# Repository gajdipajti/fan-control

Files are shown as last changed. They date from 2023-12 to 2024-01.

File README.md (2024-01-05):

# fan-control

A project for controlling 2, 3, and 4 wire DC fans using an Arduino Nano or a Raspberry Pi. It also integrates into munin monitoring. Funded by the [Free Software Foundation Hungary](https://fsf.hu/). The code is under [GPLv3](https://choosealicense.com/licenses/gpl-3.0/). Schematics, drawings, circuit diagrams, and the documentation is under [CC BY-SA-4.0](https://creativecommons.org/licenses/by-sa/4.0/). If you have an idea about how to improve the project, just file an issue and contribute.

## Pages

* [Bill Of Materials](bom/billofmaterials-nano.md)
* [Datasheet Archive](bom/datasheets.md)
* [KiCad and Fritzing](circuits/)

## Wiki

In **hungarian** and in **english**: [wiki](https://github.com/gajdipajti/fan-control/wiki)

## Fan Control Nano - Schematic

*Note: There are multiple solutions displayed here, only implement the needed ones.*

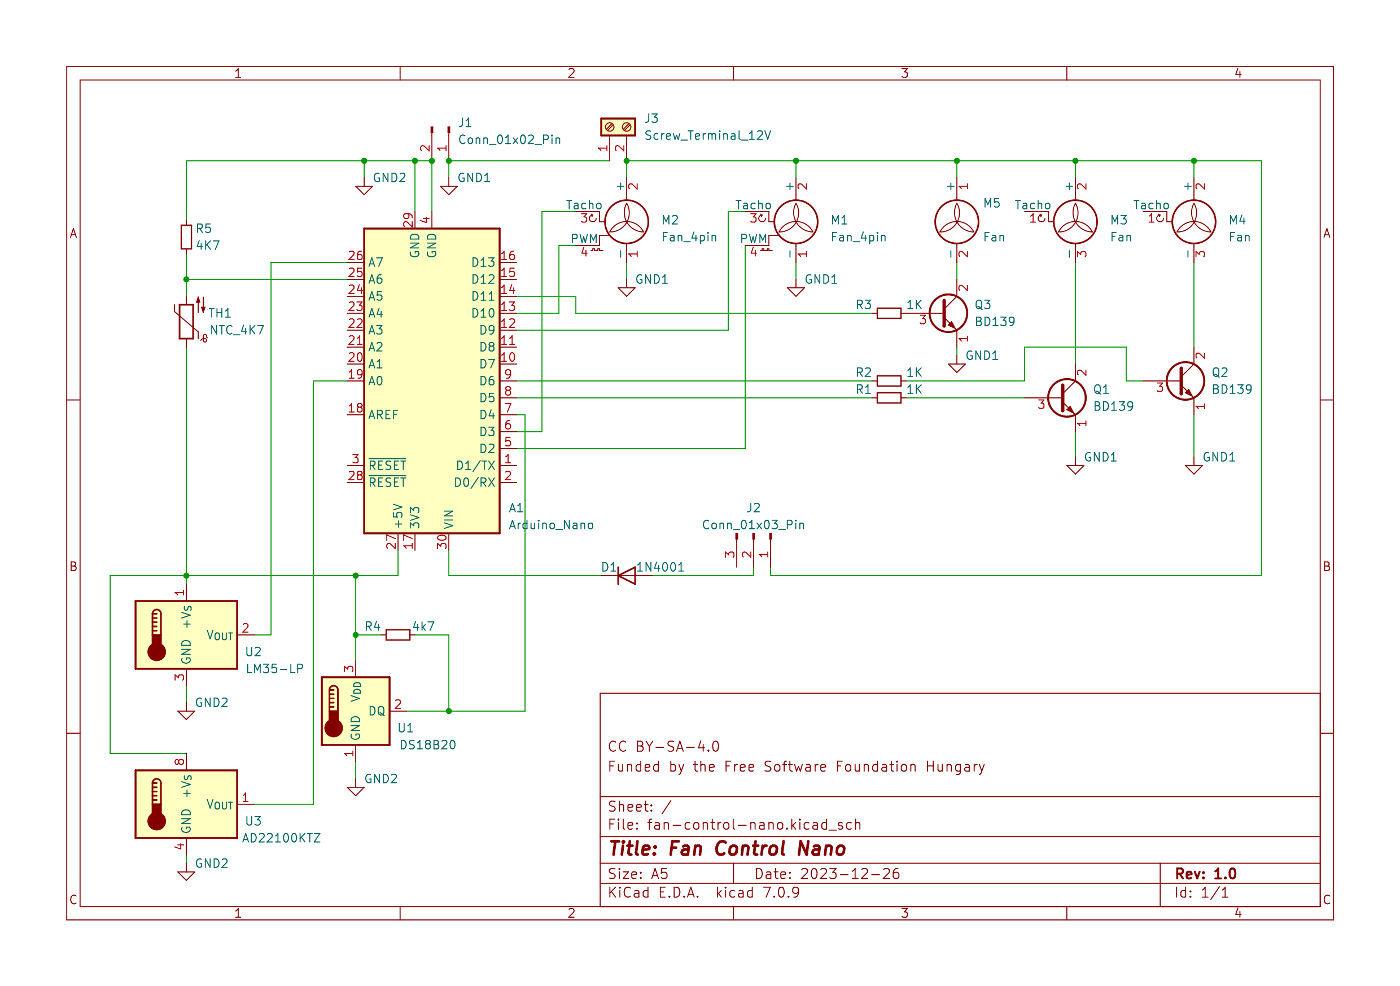
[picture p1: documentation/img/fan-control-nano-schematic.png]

How to start placing the components
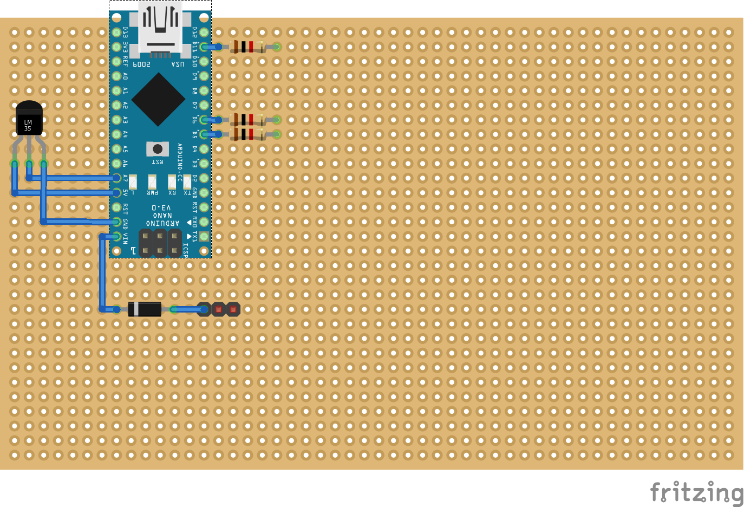
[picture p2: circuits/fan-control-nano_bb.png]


## Fan Control Nano - Code

* [Arduino Nano Code](fan-control-nano/fan-control-nano.ino)

### Serial communication

* 115200 bps
* Main Functions:
  * **pwm?**             - GET all PWM outputs
  * **pwm[A-F]?**        - GET PWM output
  * **pwm[A-F]p**        - SET PWM output to pilot mode
  * **pwm[A-F][0-255]**  - SET PWM output manually
  * **rpm[C,D]?**        - GET RPM output from 4-wire fans
  * **t?**               - GET measured temperature
  * **t[A,D,L,N]?**      - GET measured temperature from selected source
  * **ts?**              - GET temperature source (example Dallas 1-wire)
  * **tsa?**             - GET all available temperature sources
* Calibration Functions:
  * **Ch[L,H,C][A-F]?**        - GET LOW HIGH temperature for a channel
  * **Ch[L,H,C][A-F][0-100]**  - SET LOW HIGH temperature for a channel
  * **p[L,H][A-F]?**           - GET LOW HIGH PWM speed for a channel
  * **p[L,H][A-F][0-255]**     - SET LOW HIGH PWM for a channel
* Misc Func:
  * **hrs?**           - get board uptime [%d:%H:%M:%S]
  * **ver?**           - HW board version number
  * **cbn?**           - CODE build version number
  * **?**              - Ping, Are You There?  + Flash a LED

## Fan Control RPi - Schematic

*Note: There are multiple solutions displayed here, only implement the needed ones.*

*Note: Under testing.*

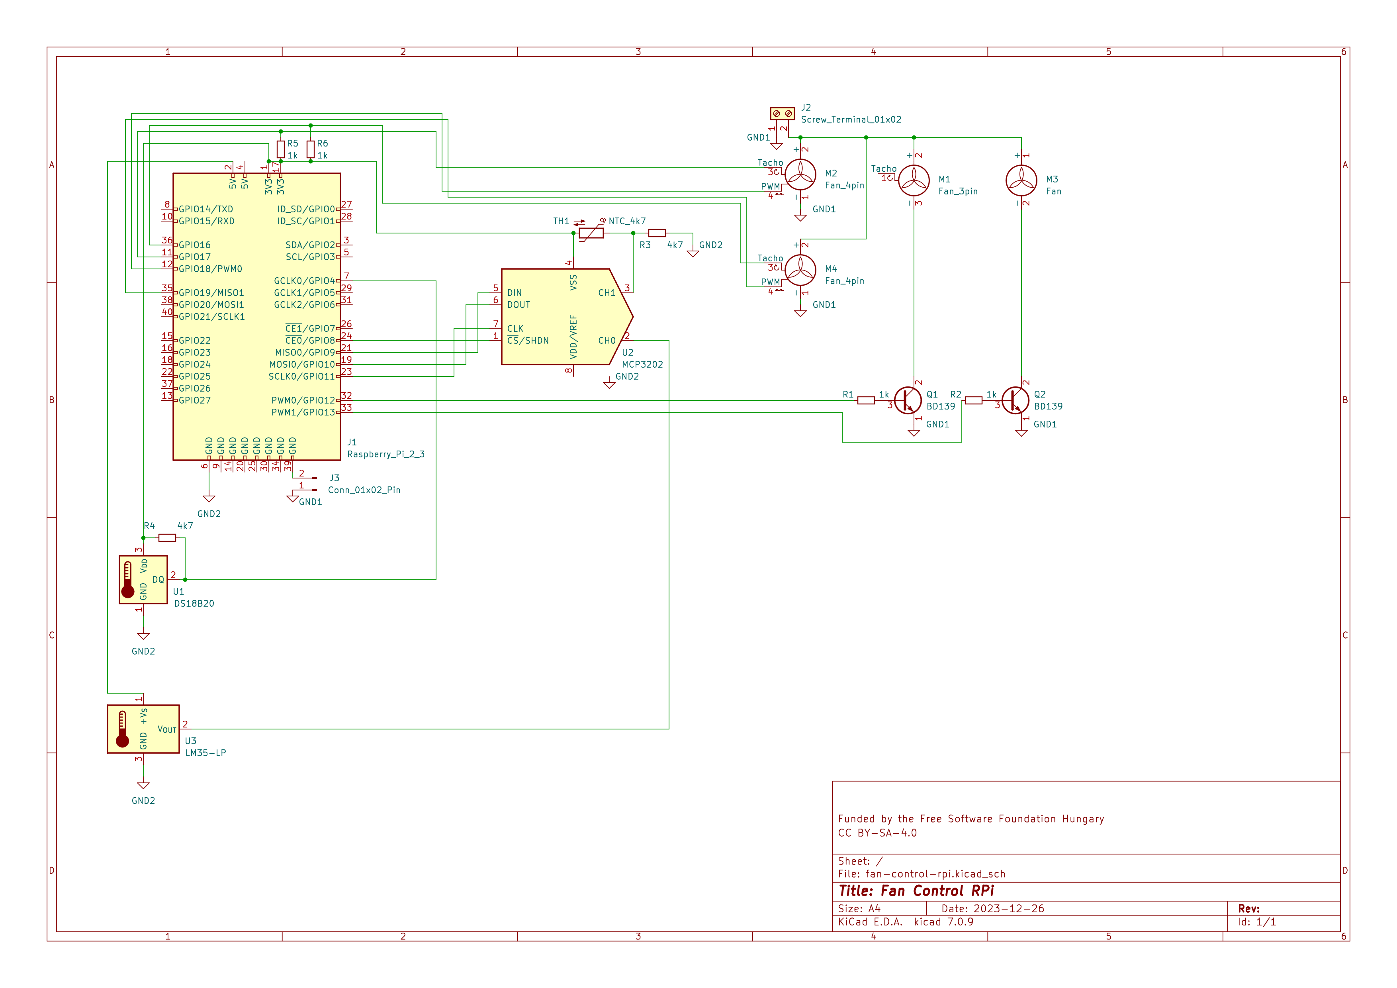
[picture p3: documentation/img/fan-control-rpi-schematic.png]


## Planned updates

* External ADC experiments
* Other board support (RP2040, Attiny85, ...)
* Without machine spirit (no microcontroller)

## References

* [Arduino Language Reference](https://www.arduino.cc/reference/en/)
  * [attachInterrupt()](https://www.arduino.cc/reference/en/language/functions/external-interrupts/attachinterrupt/)
  * [interrupts](http://gammon.com.au/interrupts)
  * [libraries](https://www.arduino.cc/reference/en/libraries/)
* [Arduino Nano](https://docs.arduino.cc/hardware/nano)
* [1-wire protocol](https://docs.arduino.cc/learn/communication/one-wire)
* [Raspberry Pi documentation](https://www.raspberrypi.com/documentation/computers/raspberry-pi.html)
* [Raspberry gpiozero](https://gpiozero.readthedocs.io/en/stable/index.html)
  * [gpiozero - pwmoutput](https://gpiozero.readthedocs.io/en/stable/api_output.html#pwmoutputdevice)
* [Raspberry Pi Zero 2 W Pinout](https://linuxhint.com/raspberry-pi-zero-2w-pinout/)
* [RPI Zero 2W Board Layout](https://www.etechnophiles.com/rpi-zero-2w-board-layout-pinout-specs-price/)

### Free Software used in this project

*Note: I only mention software that can be downloaded and installed.*

* [LibreOffice Writer](https://www.libreoffice.org/) - documentation
* [Visual Studio Code](https://code.visualstudio.com/) - documentation
  * [Markdown All in One](https://marketplace.visualstudio.com/items?itemName=yzhang.markdown-all-in-one)
  * [Markdown PDF](https://marketplace.visualstudio.com/items?itemName=yzane.markdown-pdf)
  * [markdownlint](https://marketplace.visualstudio.com/items?itemName=DavidAnson.vscode-markdownlint)
  * [Remote - SSH](https://marketplace.visualstudio.com/items?itemName=ms-vscode-remote.remote-ssh)
  * [Remote - SSH: Editing Configuration Files](https://marketplace.visualstudio.com/items?itemName=ms-vscode-remote.remote-ssh-edit)
  * [Remote Explorer](https://marketplace.visualstudio.com/items?itemName=ms-vscode.remote-explorer)
  * [Winter is Coming Theme](https://marketplace.visualstudio.com/items?itemName=johnpapa.winteriscoming) - Dark Blue
  * [Cyberpunk Theme](https://marketplace.visualstudio.com/items?itemName=max-SS.cyberpunk) - UMBRA Protocol
  * [Code Spell Checker](https://marketplace.visualstudio.com/items?itemName=streetsidesoftware.code-spell-checker)
  * [isort](https://marketplace.visualstudio.com/items?itemName=ms-python.isort)
  * [Pylance](https://marketplace.visualstudio.com/items?itemName=ms-python.vscode-pylance)
  * [Python](https://marketplace.visualstudio.com/items?itemName=ms-python.python)
* [Arduino IDE](https://www.arduino.cc/en/software) - Arduino code
  * [OneWire](https://www.arduino.cc/reference/en/libraries/onewire/)
  * [DallasTemperature](https://www.arduino.cc/reference/en/libraries/dallastemperature/)
* [KiCad](https://www.kicad.org/download/) - schematics
* [Fritzing](https://github.com/fritzing/fritzing-app/releases/tag/CD-548) - schematics
* [GNU Octave](https://octave.org/) - drawing graphs, advanced calculations
* [Qalculate!](http://qalculate.github.io/) - basic calculation

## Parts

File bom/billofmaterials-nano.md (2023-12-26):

# Bill Of Materials for the Arduino Nano and Raspberry Pi based fan controller

All the materials except the Arduino Nano v3 and the Raspberry Pi was bought from a local supplier: [Robotron Electronika](https://www.ret.hu/) - [pdf catalogue](https://www.ret.hu/FlippingBook/files/assets/downloads/files/RETKAT2012.pdf)

I also included RS links, where possible

## Arduino and Board

* 1x Arduino Nano v3 - [welectron AI-100005](https://www.welectron.com/Arduino-Nano_1), [RS 6961667](https://uk.rs-online.com/web/p/products/6961667/) - 19.99 Euro/piece - (can be replaced with a clone)
* 1x female header BL1-036-G700-95 - [RET 53-03-04](https://www.ret.hu/shop/product/e-tec/36g-buchsenleiste_53-03-04) - 1199 HUF/piece
* 1x 1N 4001 diode - [RET 19-00-01](https://www.ret.hu/shop/product/diotec/1n-4001_19-00-01), [RS 628-8931](https://uk.rs-online.com/web/p/schottky-diodes-rectifiers/6288931) - 18 HUF

## Raspberry Pi and Board

* Raspberry Pi Zero 2 W - [welectron RP1-120008](https://www.welectron.com/Raspberry-Pi-Zero-2-W_1) - 22.90 Euro/piece
* 1x male-female header BE2-040-S161-55 [RET 53-10-01](https://www.ret.hu/shop/product/e-tec/2-x-20g-16mm-buchsenleiste_53-10-01) - 1439 HUF/piece
* 1x male header SL2-050-S116/01-55 [RET 53-00-14](https://www.ret.hu/shop/product/e-tec/2-x-25g-stiftleiste_53-00-14) - 239 HUF/piece
* 1x MCP3201 single channel A/D converter [RET 38-31-67](https://www.ret.hu/shop/product/microchip/mcp-3201-ci-p_38-31-67) - 2999 HUF/piece (_if needed_)

## Board

* 1x H25PR050 single sided proto board - [RET 75-00-15](https://www.ret.hu/shop/product/rademacher/h25pr050_75-00-15) - 575 HUF/piece
* 1x male header SL1-036-SH116/01-55 - [RET 53-03-27](https://www.ret.hu/shop/product/e-tec/36g-stiftleiste_53-03-27) - 179 HUF/piece
* 2x Jumper - [RET 53-14-29](https://www.ret.hu/shop/product/taiwan-king-pin-terminal/jumper-zart-fekete_53-14-29) - 29 HUF/piece
* 1x terminal [RET 53-05-69](https://www.ret.hu/shop/product/ptr-messtechnik/ak-500-2v_53-05-69) - 114 HUF/piece

## Temperature sensing

*Note: One sensor is enough.*

* 2x 4K7 Ohm 1% Resistor - [RET 02-02-39](https://www.ret.hu/shop/product/yageo/4-7-kohm-0-66w-1-rm4_02-02-39), [RS 199-7654](https://uk.rs-online.com/web/p/through-hole-resistors/1997654) - 18 HUF/piece
* 1x DS18B20 sensor - [RET 38-22-36](https://www.ret.hu/shop/product/dallas/ds-18b20_38-22-36) - 1260 HUF/piece
* 1x NTC 4K7 3950 thermistor - [RET 09-00-34](https://www.ret.hu/shop/product/tdk-epcos/4-7-kohm-ntc-rm2-d-5-5mm_09-00-34), [RS 191-2257](https://uk.rs-online.com/web/p/thermistor-ics/1912257) - 336 HUF/piece
* 1x LM35 sensor - [RET 38-06-26](https://www.ret.hu/shop/product/national-semiconductor/lm-35dz-nopb_38-06-26), [533-5878](https://uk.rs-online.com/web/p/temperature-humidity-sensor-ics/5335878) - 1319 HUF/piece

## Fan interfacing

* 3x 1K Ohm 5% Resistor - [RET 01-00-73](https://www.ret.hu/shop/product/yageo/1-kohm-0-25w-5-rm4_01-00-73), [RS 199-1785](https://uk.rs-online.com/web/p/through-hole-resistors/1991785P) - 6 HUF/piece
* 3x NPN Transistor BD139-16 - [RET 24-03-30](https://www.ret.hu/shop/product/continental-devices/bd-139-16-n_24-03-30), [RS 686-8063](https://uk.rs-online.com/web/p/bipolar-transistors/6868063) - 106 HUF/piece
* 2x 4 pin fan header - [RET 53-32-25](https://www.ret.hu/shop/product/molex/22-27-2041_53-32-25), [RS 483-8483](https://uk.rs-online.com/web/p/products/4838483/)  - 478 HUF/piece
* 3x 3 pin fan header - [RET 53-34-30](https://www.ret.hu/shop/product/molex/22-27-2031_53-34-30), [RS 483-8477](https://uk.rs-online.com/web/p/products/4838477/)
* 3x 2 pin fan header - [RET 53-34-29](https://www.ret.hu/shop/product/molex/22-27-2021_53-34-29), [RS 483-8461](https://uk.rs-online.com/web/p/products/4838461/)

## RET Cart for the Nano version (in hungarian)

| Sorszám | Termékkód | Termék | Egységár (Nettó) | Egységár (Bruttó) | Mennyiség | Összesen (Nettó) | Összesen (Bruttó) |
| --- | --- | --- | --- | --- | --- | --- | --- |
| 1 | [09-00-34](https://www.ret.hu/shop/product/tdk-epcos/4-7-kohm-ntc-rm2-d-5-5mm_09-00-34) | 4.7 KOhm, NTC RM2 D=5,5mm | 264.57 HUF | 336 HUF | 1 | 264.57 HUF | 336 HUF |
| 2 | [75-00-15](https://www.ret.hu/shop/product/rademacher/h25pr050_75-00-15) | H25PR050 | 452.59 HUF | 574.79 HUF | 1 | 452.59 HUF | 574.79 HUF |
| 3 | [38-22-36](https://www.ret.hu/shop/product/dallas/ds-18b20_38-22-36) | DS 18B20+ | 992.12 HUF | 1259.99 HUF | 1 | 992.12 HUF | 1259.99 HUF |
| 4 | [24-03-30](https://www.ret.hu/shop/product/continental-devices/bd-139-16-n_24-03-30) | BD 139-16 \*N | 83.15 HUF | 105.6 HUF | 3 | 249.45 HUF | 316.8 HUF |
| 5 | [02-02-39](https://www.ret.hu/shop/product/yageo/4-7-kohm-0-66w-1-rm4_02-02-39) | 4.7 KOhm 0.66W 1% RM4 | 14.17 HUF | 18 HUF | 2 | 28.34 HUF | 35.99 HUF |
| 6 | [01-00-73](https://www.ret.hu/shop/product/yageo/1-kohm-0-25w-5-rm4_01-00-73) | 1 KOhm 0.25W 5% RM4 | 4.72 HUF | 5.99 HUF | 3 | 14.16 HUF | 17.98 HUF |
| 7 | [19-00-01](https://www.ret.hu/shop/product/diotec/1n-4001_19-00-01) | 1N 4001 | 14.17 HUF | 18 HUF | 1 | 14.17 HUF | 18 HUF |
| 8 | [53-03-04]((https://www.ret.hu/shop/product/e-tec/36g-buchsenleiste_53-03-04)) | 36G Buchsenleiste | 943.95 HUF | 1198.82 HUF | 1 | 943.95 HUF | 1198.82 HUF |
| 9 | [53-14-29](https://www.ret.hu/shop/product/taiwan-king-pin-terminal/jumper-zart-fekete_53-14-29)  | JUMPER zárt fekete | 22.68 HUF | 28.8 HUF | 2 | 45.36 HUF | 57.61 HUF |
| 10 | [53-05-69](https://www.ret.hu/shop/product/ptr-messtechnik/ak-500-2v_53-05-69) | AK 500/2V | 89.76 HUF | 114 HUF | 1 | 89.76 HUF | 114 HUF |
| 11 | [38-06-26](https://www.ret.hu/shop/product/national-semiconductor/lm-35dz-nopb_38-06-26) | LM 35DZ/NOPB | 1038.42 HUF | 1318.79 HUF | 1 | 1038.42 HUF | 1318.79 HUF |
| 12 | [53-32-25](https://www.ret.hu/shop/product/molex/22-27-2041_53-32-25) | 22-27-2041 | 188.03 HUF | 238.8 HUF | 2 | 376.06 HUF | 477.6 HUF |
| 13 | [53-34-30](https://www.ret.hu/shop/product/molex/22-27-2031_53-34-30) | 22-27-2031 | 0 HUF | 0 HUF | 3 | 0 HUF | 0 HUF |
| 14 | [53-34-29]((https://www.ret.hu/shop/product/molex/22-27-2021_53-34-29)) | 22-27-2021 | 0 HUF | 0 HUF | 3 | 0 HUF | 0 HUF |
| 15 | [53-03-27](https://www.ret.hu/shop/product/e-tec/36g-stiftleiste_53-03-27) | 36G Stiftleiste | 140.79 HUF | 178.8 HUF | 1 | 140.79 HUF | 178.8 HUF |
| | | | | | | | |
| | | | | | | Nettó összesen | Bruttó összesen |
| | | | | | | 4650 HUF | 5905 HUF |

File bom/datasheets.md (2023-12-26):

# Datasheet Archive for the project

Note: this is just a datasheet archive of the electronic components that are mentioned

## Fan Control Nano

* Diode [1N4001](datasheet-archive-nano/1n4001.pdf)
* Transistor [BD139](datasheet-archive-nano/bd139.pdf) or [BD139](datasheet-archive-nano/bd135_37_39.pdf)
* Resistor 4k7 1% [Yageo MF0207FTE52-4K7](datasheet-archive-nano/Yageo_LR_MF0207FTE52-4K7.pdf)
* Resistor 1k 5% [Yageo CFR-25JT-52-1K](datasheet-archive-nano/Yageo_LR_CFR-25JT-52-1K.pdf)
* Temperature sensor [Maxim DS18B20](datasheet-archive-nano/DS18B20.pdf)
* Thermistor [NTC 4k7 3950](datasheet-archive-nano/Epcos_B57164K.pdf)
* Temperature sensor [TI LM35DZ](datasheet-archive-nano/lm35.pdf)

## Fan Control RPi

* Diode [1N4001](datasheet-archive-nano/1n4001.pdf)
* Transistor [BD139](datasheet-archive-nano/bd139.pdf) or [BD139](datasheet-archive-nano/bd135_37_39.pdf)
* Resistor 4k7 1% [Yageo MF0207FTE52-4K7](datasheet-archive-nano/Yageo_LR_MF0207FTE52-4K7.pdf)
* Resistor 1k 5% [Yageo CFR-25JT-52-1K](datasheet-archive-nano/Yageo_LR_CFR-25JT-52-1K.pdf)
* Temperature sensor [Maxim DS18B20](datasheet-archive-nano/DS18B20.pdf)
* Thermistor [NTC 4k7 3950](datasheet-archive-nano/Epcos_B57164K.pdf)
* Temperature sensor [TI LM35DZ](datasheet-archive-nano/lm35.pdf)
* A/D Converter Microchip [MCP3002](datasheet-archive-misc/mcp3002.pdf)

## Microchip A/D converters (SPI)

* [MCP3001](datasheet-archive-misc/mcp3001.pdf)
* [MCP3002](datasheet-archive-misc/mcp3002.pdf)
* [MCP3004/8](datasheet-archive-misc/mcp300x.pdf)
* [MCP3201](datasheet-archive-misc/mcp3201.pdf)
* [MCP3202](datasheet-archive-misc/mcp3202.pdf)
* [MCP3204/8](datasheet-archive-misc/mcp320x.pdf)

## Other components that were considered

* Temperature sensor [AD22100](datasheet-archive-misc/AD22100.pdf) - only positive values, large range
* Transistor [2N3904](datasheet-archive-misc/2N3903-D.PDF) - less power
* Voltage reference 1.235 Volt [LM385-1.2](datasheet-archive-misc/LM285-D.PDF)
* Voltage reference 2.5 Volt [LM385-2.5](datasheet-archive-misc/LM285-D.PDF) or [LM385-2.5-N](datasheet-archive-misc/lm285-2.5-n.pdf)
* Voltage reference 5.0 Volt [LM336](datasheet-archive-misc/lm336-5.0.pdf)
* Voltage converter 5.0 Volt 1 Amp [L7805](datasheet-archive-misc/L7805.pdf)
* Voltage converter 5.0 Volt 1 Amp [LM2940-5](datasheet-archive-misc/lm2940-n.pdf)

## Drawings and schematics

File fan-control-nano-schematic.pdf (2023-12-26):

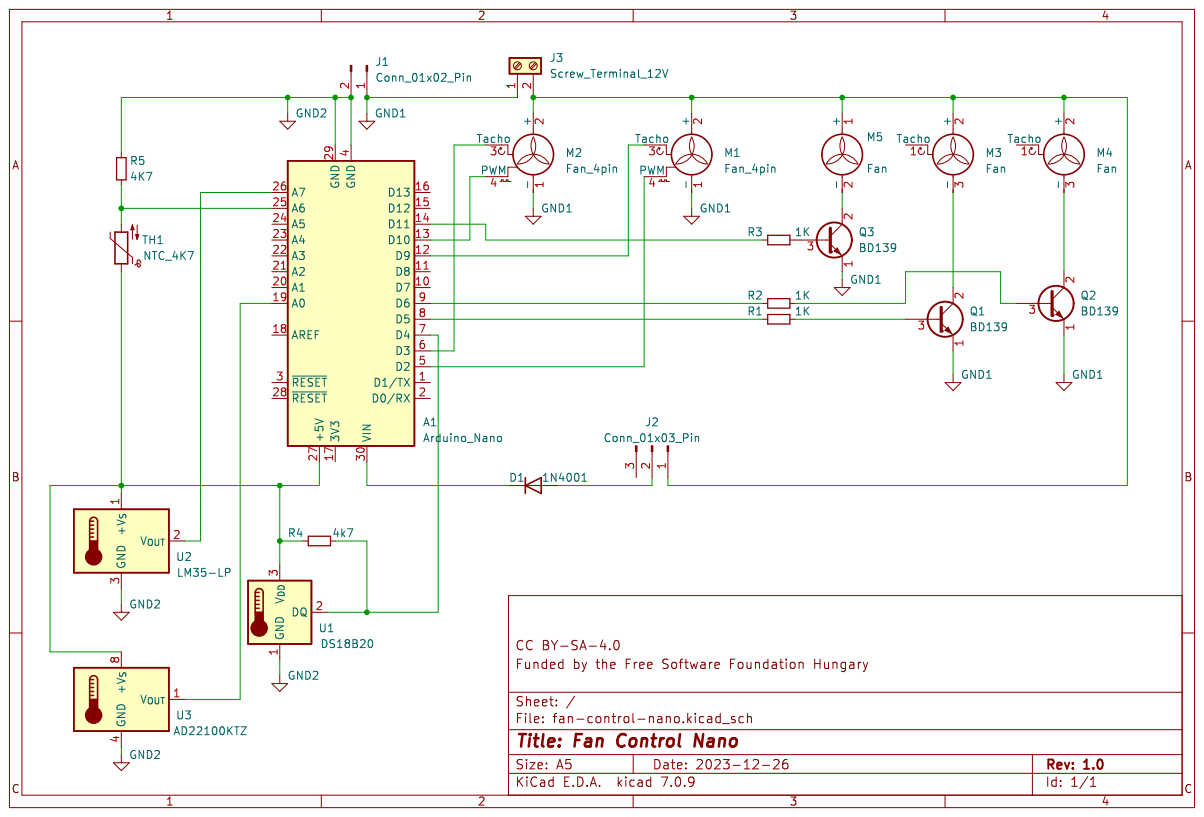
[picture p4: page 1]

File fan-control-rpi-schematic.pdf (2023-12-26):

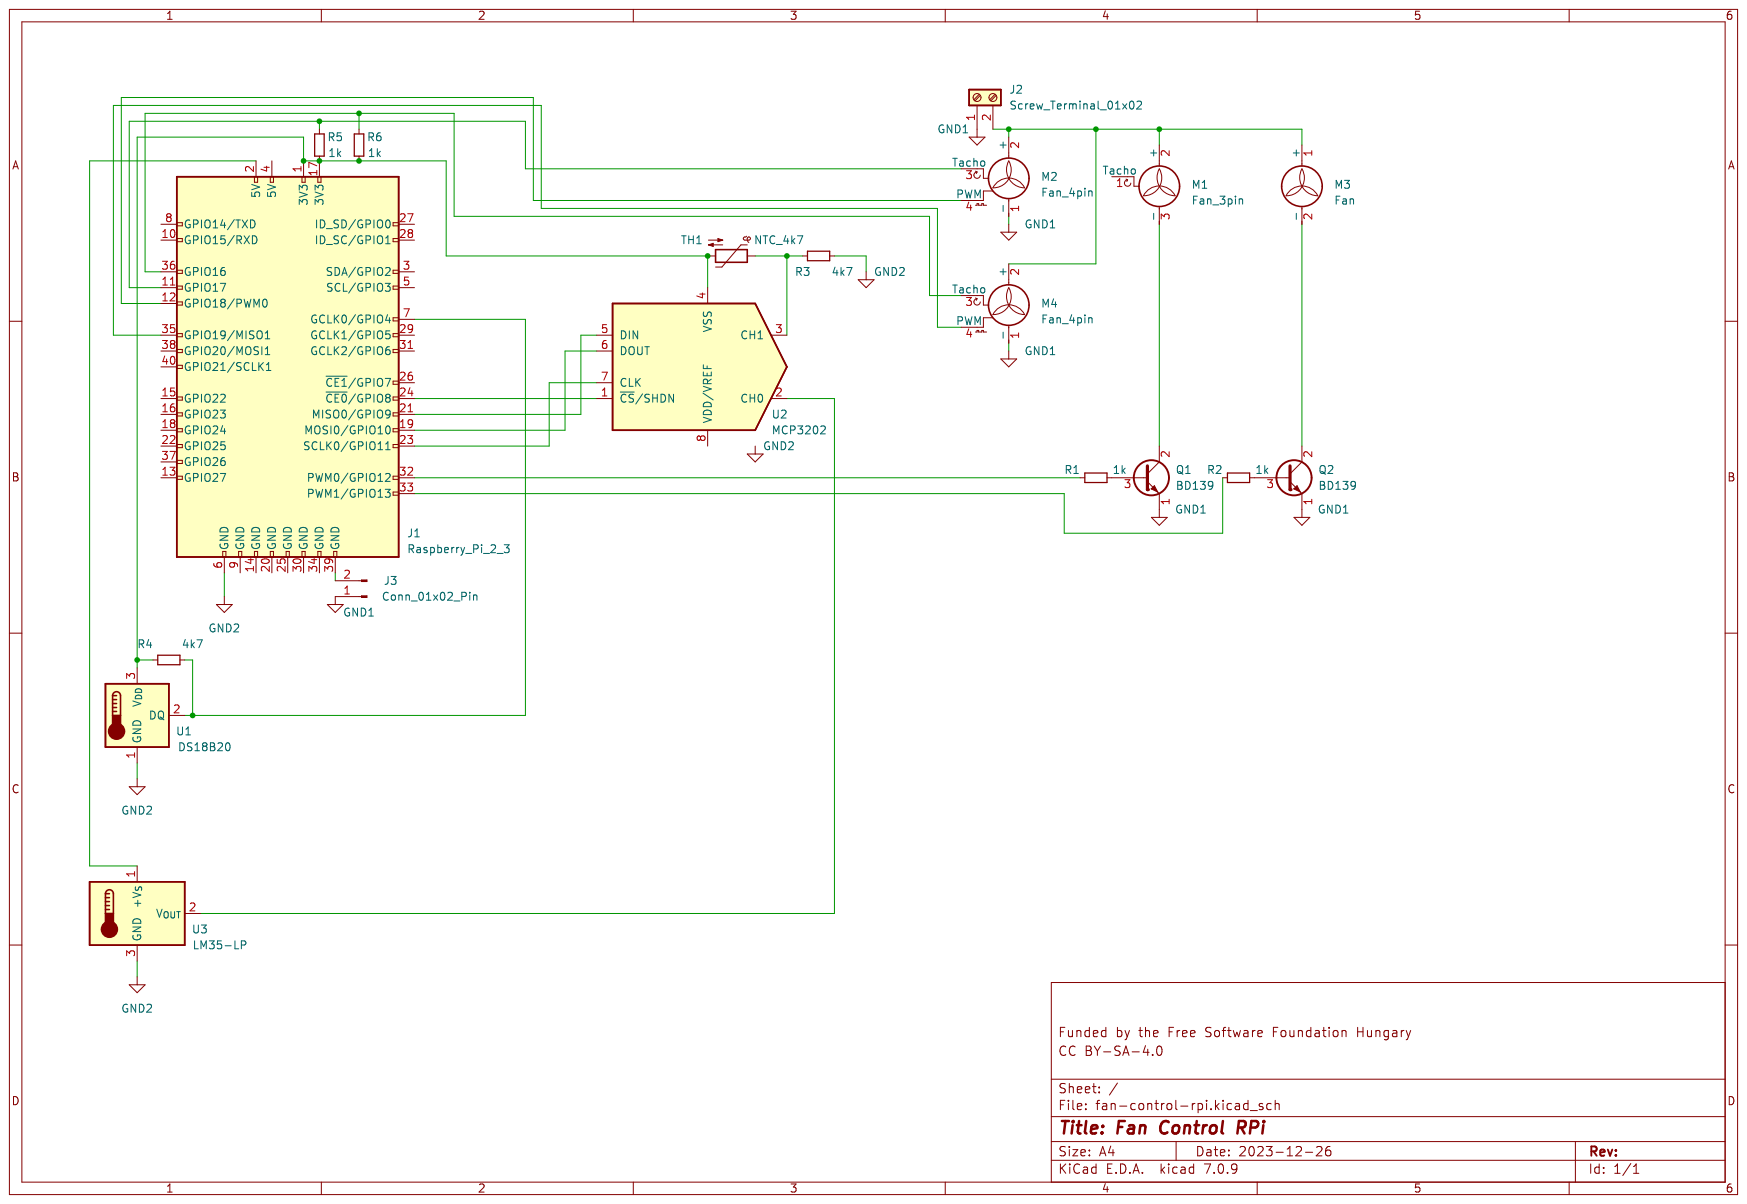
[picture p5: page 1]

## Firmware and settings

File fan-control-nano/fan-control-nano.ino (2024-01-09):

/*
  A 5 channel fan controller for 2, 3, and 4 wire fans.
  Code under GPLv3 license. Author: gajdost (gajdipajti@gmail.com)

Pin Assignment:

  Fan channels: 
   * PIN D5  (Timer0) PWM - ChA - 2 or 3 pin fans only
   * PIN D6  (Timer0) PWM - ChB - 2 or 3 pin fans only
   * PIN D9  (Timer1) PWM - ChC - configured for 4 pin fan
   * PIN D10 (Timer1) PWM - ChD - configured for 4 pin fan
   * PIN D11 (Timer2) PWM - ChE - 2, 3, or 4 pin fans
  Optional fan channel:
   * PIN D3  (Timer2) PWM - ChF - 2, 3, or 4 pin fans OR tachometer interrupt

  Detect interrupts:
   * PIN D2           Tachometer - Interrupt ChC
   * PIN D3  (Timer2) Tachometer - Interrupt ChD

  Temperature measurement (one is enough):
   * PIN D12          Dallas 1-wire DS18B20
   * PIN A7  (ADC)    LM35
   * PIN A6  (ADC)    NTC Thermistor - NTC B57164K0472K000 Rn: 4k7 Ohm; K = 3950; Rs = 4k7 Ohm
   * PIN A0  (ADC)    AD22100KTZ
  Optional temperature pins:
   * PIN A1  (ADC) - tE
   * PIN A2  (ADC) - tD
   * PIN A3  (ADC) - tC

  Optional display pins:
   * PIN D4        - button press
   * PIN A4  (LCD) - reserved for I2C
   * PIN A5  (LCD) - reserved for I2C

  Heartbeat pin:
   * PIN D13 (LED) - heartbeat

Serial Commands:

  Main Functions:
   * fan?             - GET installed fans, all information
   * pwm?             - GET all PWM outputs
   * pwm[A-F]?        - GET PWM output
   * pwm[A-F]p        - SET PWM output to pilot mode
   * pwm[A-F][0-255]  - SET PWM output manually
   * rpm[C,D]?        - GET RPM output from 4-wire fans
   * t?               - GET measured temperature
   * t[A,D,L,N]?        - GET measured temperature from selected source
   * ts?              - GET temperature source (example Dallas 1-wire)
   * tsa?             - GET all available temperature sources

  Optional Functions: [when extra circuit is present]
   * lcd[?,0-4] - GET/SET LCD Backlight; Update LCD
  Calibration Functions:
   * Ch[L,H,C][A-F]?        - GET LOW HIGH temperature for a channel
   * Ch[L,H,C][A-F][0-100]  - SET LOW HIGH temperature for a channel
   * p[L,H][A-F]?           - GET LOW HIGH PWM speed for a channel
   * p[L,H][A-F][0-255]     - SET LOW HIGH PWM for a channel
  Misc Func:
   * hrs?           - get board uptime [%d:%H:%M:%S]
   * ver?           - HW board version number
   * cbn?           - CODE build version number
   * ?              - Ping, Are You There?  + Flash a LED
   * stream         - flip ON/OFF stream mode
   * m?             - GET information for munin setup          
   * m!             - GET information for munin monitoring
*/
// Ref: http://www.gammon.com.au/tips
// #define ARRAY_SIZE(x) (sizeof(x) / sizeof((x)[0]))

#include <Wire.h> 
#include <uptime.h>
#include <OneWire.h>
#include <DallasTemperature.h>
// #include <LiquidCrystal_I2C.h>
// LiquidCrystal_I2C lcd(0x27,16,2);  // set the LCD address to 0x27 for a 16 chars and 2 line display

// Fan configuration - change this
// the compiler will work out the size
const bool fanmask[] = {true, true, true, true, true};
// Variables and constants which might be checked in the GUI
const byte  swVersion = 001;
const float hwVersion = 1.0;
const char  boardSubVersion = 'A';
float time;

// Define PWM pins Channel A-E
// the compiler will work out the size
const byte pwm[] = {5, 6, 9, 10, 11};
// const byte pwmF = 3;     // Used as interrupt

// Define 2D settings array for pwm and temperature
// ROWS: Channel A-E - the compiler will work out the size of the first dimension
// COLS: manual[0-1], current[0-255], LOW[0-255], HIGH[0-255], CRITICAL[255], ...
//                                         tLOW[0-85], tHIGH[0-85], tCRITICAL[85]
byte preset[][8] = {
  {0, 128, 30, 250, 255, 20, 30, 85},
  {0, 128, 30, 250, 255, 20, 30, 85},
  {0, 128, 30, 250, 255, 20, 60, 85},
  {0, 128, 30, 250, 255, 20, 60, 85},
  {0, 128, 30, 250, 255, 20, 60, 85}
};

// Define interrupt pins
const byte intC = 2;
const byte intD = 3;

// Store rpm values in volatile time variables
volatile unsigned long t_irpmC = 0;
volatile unsigned long tC = 0;
volatile unsigned long t_irpmD = 0;
volatile unsigned long tD = 0;
byte t0_corr = 0;

// Define temperature and lcd pins
char tempSource = 'D';      // The source of the temperature: 'N' - NTC, 'L' - LM35, 'D' - DS18B20, 'A' - AD22100KTZ, ...
const byte lm35 = A7;       // if an LM35 is connected
const byte ntc  = A6;       // if an NTC is connected
const byte ad22100 = A0;    // if an AD22100KTZ is connected
const byte OneWireBus = 4;  // Data wire for OneWire
bool dallasPresent = true;  // store dallas sensor status

// Define the thermistor
// Ref for external library: https://www.arduino.cc/reference/en/libraries/thermistor/
// NTC B57164K0472K000 R25: 4k7 Ohm; K = 3950; Rs = 4k7 Ohm
float R25_ntc = 4700.00;
float K_ntc = 3950.00;
float Rs_ntc = 4700.00;

// Configure OneWire
OneWire oneWire(OneWireBus);
DallasTemperature sensors(&oneWire);
DeviceAddress insideThermometer;

// A4 -> LCD SDA
// A5 -> LCD SCL
// A8 is connected to the internal temperature sensor.

// For LCD
// bool lcdState = HIGH;

// For serial communication.
String inputString = "";        // a string to hold incoming data
bool stringComplete = false;    // whether the string is complete
bool automode = false;           // enable auto mode

// Wait mode
short waitPeriod = 1000;
unsigned long startWait = 0;

void setup() {  // The initial setup, that will run every time when we connect to the Arduino via serial.
                // To disable the auto reset, change the switch position on the board.

  pinMode(LED_BUILTIN, OUTPUT); digitalWrite(LED_BUILTIN, HIGH);
  
  Serial.begin(115200);
  
  // Voltage channel outputs, it's not needed for analogWrite, but just in case.
  // https://www.arduino.cc/reference/en/language/functions/analog-io/analogwrite/
  pinMode(pwm[0], OUTPUT); analogWrite(pwm[0], LOW);
  pinMode(pwm[1], OUTPUT); analogWrite(pwm[1], LOW);
  pinMode(pwm[2], OUTPUT); analogWrite(pwm[2], LOW);
  pinMode(pwm[3], OUTPUT); analogWrite(pwm[3], LOW);
  pinMode(pwm[4], OUTPUT); analogWrite(pwm[4], LOW);
  // pinMode(pwmF, OUTPUT); analogWrite(pwmF, LOW);  // Not used

  // Attach interrupts
  // Ref: https://www.arduino.cc/reference/en/language/functions/external-interrupts/attachinterrupt/
  pinMode(intC, INPUT_PULLUP);
  pinMode(intD, INPUT_PULLUP);
  attachInterrupt(digitalPinToInterrupt(intC), tachC, FALLING);
  attachInterrupt(digitalPinToInterrupt(intD), tachD, FALLING);

  // Temperature input
  // https://www.arduino.cc/reference/en/language/functions/analog-io/analogreference/
  // analogReference(INTERNAL);    // set AREF to 1.1 V
  pinMode(ntc,  INPUT);
  pinMode(lm35, INPUT);
  pinMode(ad22100, INPUT);

  // Copied the relevant part from here: http://playground.arduino.cc/Code/PwmFrequency
  // Also refs: 
  // * https://forum.arduino.cc/t/varying-the-pwm-frequency-for-timer-0-or-timer-2/16679/3
  // * https://docs.arduino.cc/tutorials/generic/secrets-of-arduino-pwm
  t0_corr = 6;                            // Correction for Timer0 change
  TCCR0B = TCCR0B & 0b11111000 | 0x01;    // The Arduino uses Timer 0 internally for the millis() and delay() functions
  TCCR1B = TCCR1B & 0b11111000 | 0x01;    // Change PWM Frequency for Timer1.  f=~31kHz
  // TCCR2B = TCCR2B & 0b11111000 | 0x01;    // Change PWM Frequency for Timer2.  f=~31kHz

  // delay(1000);
  // For Serial Communication
  inputString.reserve(128);   // reserve 128 bytes for the inputString

  // OneWire setup;
  if (!sensors.getAddress(insideThermometer, 0)) {
    Serial.println("Unable to find address for Device 0");
    dallasPresent = false;
  } else {
    sensors.setResolution(insideThermometer, 10);
  }

  digitalWrite(LED_BUILTIN, LOW);
}

float ntcTemp() {
    float ADCntc = analogRead(ntc);
    // Calculate the measured resistance using the reference series resistance.
    float RT_ntc = Rs_ntc / ((1024.00/ADCntc) - 1.00);
    // Calculate the 1/T from the Steinhart equation. Note: T0 is in Kelvin.
    float recT = 1.00/(273.00+25.00) + log(RT_ntc/R25_ntc)/K_ntc;
    // Convert to Celsius.
    return 1.00/recT - 273.00; 
}

float ad22100Temp() {
  // AD22100KTZ: V_out = (V_ref/5V) * (1,375 V + 0,0225 V/°C * T)
  //             T = (V_out–1,375V)/0,0225 V/°C
  //             T = (adc*(V_ref/1024) – 1,375 V) /0,0225 V/°C

  // If AREF = 5000 mV
  // Resolution: 0.217°C;
  // Range: -50°C - 150°C [51 - 973 ADC] 

  float adc = analogRead(ad22100);
  float V_out = adc*(5000.00/1024.00);
  return (V_out - 1.375)/0.0225;
}

float lm35Temp() {
  // LM35DZ: 10mV/°C -> (adc*(aref/1024))/10
  
  // Settings for AREF = 1100 mV
  // Resolution: 0.11°C; Precision +/- 1 °C
  // Range: 0°C - 110°C [0 - 1023 ADC]
  
  // Settings for AREF = 5000 mV
  // Resolution: 0.49°C; Precision +/- 1 °C
  // Range: 0°C - 110°C [0 - 225 ADC]

  float tmV = analogRead(lm35);
  return tmV*(500.00/1024.00);
}

float ds18Temp() {
  if (dallasPresent) {
    // call sensors.requestTemperatures() to issue a global temperature 
    // request to all devices on the bus
    sensors.requestTemperatures(); // Send the command to get temperatures
    // printTemperature(insideThermometer); // Use a simple function to print out the data
    float tempC = sensors.getTempC(insideThermometer);
    return tempC;
  } else {
    return 80.00;   // In case of problem the output should be
  }
}

float getTemperature(char Source) {
  // NOTE: Implement here other sources.
  switch (Source) {
    case 'N':
      return ntcTemp();  break;
    case 'L':
      return lm35Temp(); break;
    case 'D':
      return ds18Temp(); break;
    case 'A':
      return ad22100Temp(); break;
    default:
      break;
  }
}

void tachC() {
  unsigned long time=micros();    // Store current microseconds.
  // Calculate the time difference to last call. This might not be safe.
  t_irpmC = time - tC;
  tC = time;                      // Store last call time.
}

void tachD() {
  unsigned long time=micros();    // Store current microseconds.
  // Calculate the time difference to last call. This might not be safe.
  t_irpmD = time - tD;
  tD = time;                      // Store last call time.
}

unsigned long toRPM(unsigned long irpm, byte correction) {
  // Calculate actual Rounds Per Minute
  unsigned long rpm = 60000000/irpm;
  return (rpm>1 && irpm > 0) ? rpm << correction : 0;
}

void loop() {
  if (stringComplete) {
    // Serial.println(inputString);  // Echo
    if (inputString.startsWith("t")) {
      switch(inputString.charAt(1)) {
        case '?':
          Serial.println(getTemperature(tempSource)); break;
        case 's':
          Serial.println(tempSource);          // Display source
          if (dallasPresent) { 
            Serial.print("Device DS18B20 Address: ");
            for (byte jdx = 0; jdx < 8; jdx++) {
              Serial.print(insideThermometer[jdx], HEX);
            }
            Serial.println(";");
          }
          break;
        case 'N':
          Serial.println(ntcTemp());  break;  // Only for debugging
        case 'L':
          Serial.println(lm35Temp()); break;  // Only for debugging
        case 'D':
          Serial.println(ds18Temp()); break;  // Only for debugging
        case 'A':
          Serial.println(ad22100Temp()); break;  // Only for debugging
        default:
          Serial.print("Syntax Error: "); Serial.println(inputString);
          break;
      }
    } else if (inputString.startsWith("pwm")) {
      if (inputString.endsWith("?")) {
        // Read current pwm settings from array.
        switch(inputString.charAt(3)) {
          case 'A':
            Serial.println(preset[0][1]); break;
          case 'B':
            Serial.println(preset[1][1]); break;
          case 'C':
            Serial.println(preset[2][1]); break;
          case 'D':
            Serial.println(preset[3][1]); break;
          case 'E':
            Serial.println(preset[4][1]); break;
          case '?':
            Serial.print(preset[0][1]); Serial.print(";");
            Serial.print(preset[1][1]); Serial.print(";");
            Serial.print(preset[2][1]); Serial.print(";");
            Serial.print(preset[3][1]); Serial.print(";");
            Serial.print(preset[4][1]); Serial.println(";"); break;
          default:
            Serial.print("Syntax Error: "); Serial.println(inputString);
            break;
        }
      } else if (inputString.endsWith("p")) {
        // Set to pilot mode from manual to auto.
        int value = constrain(inputString.charAt(3),65,69)-65;
        preset[value][0] = 0;
        Serial.println("OK");
      } else {
        // Manually set the pwm value. Set to manual mode.
        int value = constrain(inputString.charAt(3),65,69)-65;
        preset[value][1] = constrain(byte(inputString.substring(4).toInt()),0,255);
        preset[value][0] = 1;
        analogWrite(pwm[value],inputString.substring(4).toInt());
        Serial.println("OK");
      }
    } else if (inputString.startsWith("rpm")) {
      switch(inputString.charAt(3)) {
        case 'C':
          Serial.println(toRPM(t_irpmC, t0_corr)); break;
        case 'D':
          Serial.println(toRPM(t_irpmD, t0_corr)); break;
        case '?':
          Serial.print(toRPM(t_irpmC, t0_corr)); Serial.print(";");
          Serial.println(toRPM(t_irpmD, t0_corr)); break;
        default:
          Serial.print("Syntax Error: "); Serial.println(inputString);
          break;
      } 
    } else if (inputString.startsWith("fan?")) {
      // Print information about the fans
      Serial.println("fanmask"); // Change this to the bit array.
    } else if (inputString.startsWith("?")) {
      // Are you there?
      digitalWrite(LED_BUILTIN, !digitalRead(LED_BUILTIN));
      Serial.println("OK");
    } else if (inputString.startsWith("hrs?")) {
      if (t0_corr == 0) {
        // Uptime
        uptime::calculateUptime();
        Serial.print(uptime::getDays());      Serial.print(":");
        Serial.print(uptime::getHours());     Serial.print(":");
        Serial.print(uptime::getMinutes());   Serial.print(":");
        Serial.println(uptime::getSeconds());
      } else {
        Serial.println("00:00:00:00");          // Timer0 source is not good.
      }
    } else if (inputString.startsWith("cbn?")) { Serial.println(swVersion);  // Code Build Number
    } else if (inputString.startsWith("ver?")) {
      Serial.print(hwVersion, 1); Serial.println(boardSubVersion);            // Version Number + Board SubVersion
    } else if (inputString.startsWith("p")) {
      int value = constrain(inputString.charAt(2),65,69)-65;
      if (inputString.endsWith("?")) {
        // GET LOW or HIGH pwm settings.
        switch(inputString.charAt(1)) {
          case 'L':
            Serial.println(preset[value][2]); break;
          case 'H':
            Serial.println(preset[value][3]); break;
          default:
            Serial.print("Syntax Error: "); Serial.println(inputString);
            break;
        }
      } else {
        // SET LOW or HIGH pwm settings.
        // But constrain LOW between 0 and HIGH, and constrain HIGH between LOW and CRITICAL.
        switch(inputString.charAt(1)) {
          case 'L':
            preset[value][2] = constrain(byte(inputString.substring(3).toInt()), 0, preset[value][3]);
            Serial.print(preset[value][2]); 
            Serial.println(" OK"); break;
          case 'H':
            preset[value][3] = constrain(byte(inputString.substring(3).toInt()), preset[value][2], preset[value][4]);
            Serial.print(preset[value][3]); 
            Serial.println(" OK"); break;
          default:
            Serial.print("Syntax Error: "); Serial.println(inputString);
            break;
        }     
      }
    } else if (inputString.startsWith("Ch")) {
      int value = constrain(inputString.charAt(3),65,69)-65;
      if (inputString.endsWith("?")) {
        // GET LOW or HIGH pwm settings.
        switch(inputString.charAt(2)) {
          case 'L':
            Serial.println(preset[value][5]); break;
          case 'H':
            Serial.println(preset[value][6]); break;
          default:
            Serial.print("Syntax Error: "); Serial.println(inputString);
            break;
        }
      } else {
        // SET LOW or HIGH pwm settings.
        // But constrain LOW between 0 and HIGH, and constrain HIGH between LOW and CRITICAL.
        switch(inputString.charAt(2)) {
          case 'L':
            preset[value][5] = constrain(byte(inputString.substring(4).toInt()), 0, preset[value][6]);
            Serial.print(preset[value][5]); 
            Serial.println(" OK"); break;
          case 'H':
            preset[value][6] = constrain(byte(inputString.substring(4).toInt()), preset[value][5], preset[value][7]);
            Serial.print(preset[value][6]);
            Serial.println(" OK"); break;
          default:
            Serial.print("Syntax Error: "); Serial.println(inputString);
            break;
        }     
      }
    }
    // Do your thing
    inputString = ""; stringComplete = false;      //clear the string
  } else if (automode) {
    // GET temperature in float, convert to int
    // UPDATE pwm if not in manual
    // To preserve the 0.25°C precision, the temperature is multiplied by 4.
    int currentTemp = int(getTemperature(tempSource)*4);
    for (int idx = 0; idx < sizeof(fanmask); idx++) {
      if (fanmask[idx] && (preset[idx][0] == 0)) {
        // Multiply the temperature ranges by 4 also.
        preset[idx][1] = map(currentTemp, preset[idx][5]*4, preset[idx][6]*4, preset[idx][2], preset[idx][3]);
        analogWrite(pwm[idx], preset[idx][1]);
      }
    }
  } else {
    delay(1);
  }
  //serialEvent();  // Workaround for ATTiny or ATMega chips without hardware serial
}

void serialEvent() {
 // SerialEvent occurs whenever a new data comes in the hardware serial RX. This routine is run between each
 // time loop() runs, so using delay inside loop can delay response. Multiple bytes of data may be available.
  while (Serial.available()) {
    char inChar = (char)Serial.read();          // get the new byte
    if (inChar == '\r') {                       // if the incoming character is a carriage return (ASCII 13),
      stringComplete = true;                    // set a flag so the main loop can do something about it.
    } else { inputString += inChar; }           // otherwise add it to the inputString                             
  }
}

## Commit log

2023-10-16 Initial code dump
    Based on my previous works in the Arduino environment the initial code
    was forged. The basic idea is to have 5 channels for fan control. Three
    channels are for 2 or 3 wire fans, and two channels are for 4 wire
    fans. To handle the ~25 kHz requirement, Timer1 speed is changed to ~31
    kHz. For the 4 wire fans a tachometer will be implemented using the
    interrupt pins. Pins were also assigned for an optional LCD display.
    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
2023-10-16 Add placeholer Raspberry Pi Python code
2023-11-06 Batch of Arduino updates
    I continued the work on the code and on the circuit on the prototype board. Some functions were
    removed or updated. The current idea is to use more arrays and access them by index. At the
    current stage I do not want to use advanced techniques, as we have enough space and memory.
    Basically the serial communication part is complete, only the munin part is left.
    Itemized:
    * General configuration string and bool for enabling and disabling a fan channel.
    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
2023-12-23 Bill of Materials for the Nano Fan
2023-12-23 Complete the fan-control-nano arduino code.
    This can be considered feature complete.
    * Change Timer0 clock divider to run at full speed. Solves audible whining of the fans.
    * Implement tachometer functionality for 4-pin fans.
    * Add tachometer timing correction factor as a workaround for Timer0 clock changes.
    * Add NTC temperature source.
    * Add NTC temperature calculation.
    * Typo corrections.
    It compiles in old (1.8.19) and new (2.2.1) Arduino IDE. Arduino Nano v3.
    It runs on Arduino Nano v3.
    Sketch uses 13796 bytes (44%) of program storage space. Maximum is 30720 bytes.
    Global variables use 606 bytes (29%) of dynamic memory, leaving 1442 bytes for local variables. Maximum is 2048 bytes.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
    [fan-control-nano.ino]
2023-12-23 Add KiCad schematic, update README.
    [fan-control-nano.kicad_pcb, fan-control-nano.kicad_sch]
2023-12-26 New sensor support: AD22100K
    * Update README
    * Change ntcTemp() constant naming.
2023-12-26 Update nano circuit, add rpi circuit, update readme.
    [fan-control-nano.kicad_sch, fan-control-rpi.kicad_pcb, fan-control-rpi.kicad_sch]
2024-01-09 There was a serial race condition. Minor fixes.
    [fan-control-nano.ino]
